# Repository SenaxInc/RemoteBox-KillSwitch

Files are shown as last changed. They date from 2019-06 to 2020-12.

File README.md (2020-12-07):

# RemoteBox-KillSwitch

## Overview:
  * Arduino attached to a liquid level height switch.
  * Arduino attached to an engine ignition.
  * When liquid switch is triggered, a radio signal is sent to turn of the engine.

## Main Parts:
  * Arduino Uno with Radio Shield
  * DIGI xbee LoRa Radios
  * Relay Switch Module
  * Solar Panel
  * Morningstar SunKeeper-6 Charge Controller
  * Lead Acid Battery

## Wiring Diagram - Solar



## Solder Diagram



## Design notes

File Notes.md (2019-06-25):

## ToDo

  * send confirmation signal back to level monitor box, use to trigger sleep
  * sleep mode
      * see avr sleep example: https://github.com/dorkmo/ArduinoSMSTankAlarm/blob/master/TankAlarm072017.ino
      * see digi sleep mode: https://www.digi.com/resources/documentation/Digidocs/90001456-13/reference/r_wk_sleep_mode.htm
  * syncronize sleep/wake times
      * wake up every 30 minutes, broadcast till other box wakes up, do the business, then sleep for 30 minutes 

## Questions

  * can an arduino digital pin put out enough amps to power the relay module?
      * could power down relay module when not in use

## Sleep Routine

  * when transmition of kill or stay alive broadcast is complete and confirmed.
      * send "Z" to say ready for bed. When recieve "z" back, end all transmissions.
      * xbee sleep mode will engage after 2 minutes as predefined time in XCTU settings
      * arduino will go into avr sleep mode for 8 seconds at a time, keeping count.
      * after 28 minutes wakeup xbee as defined in XCTU sleep timer
      * after 30 minutes, end arduino avr sleep.
      * Broadcast "W" awake status every 1 minute using delay(). wait for "w" confirmation.
      * Broadcast status of liquid level switch. "K" to kill. "A" to stay alive.
      * Wait for Confirmation of "k", "a", or "E" for error. 
      * Broadcast "Z"

## Related Links

  * http://opensourceecology.org/wiki/MicroTrac_Controller_v17.10/Code

## XBEE SETTINGS

  * NI - Name for Module
  * Sleep using arduino pin signal:
      * SM - 1
  * Sleep using timer:
      * SO - 8
      * ST - 493E0
      * SP - 249F0

  * http://docs.digi.com/display/XBeeArduinoCodingPlatform/Sleep+mode
  * https://www.digi.com/resources/documentation/Digidocs/90001477/reference/r_cmd_so.htm
  * http://cms.digi.com/resources/documentation/digidocs/90001537/references/r_xbee_sleeping_problems.htm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

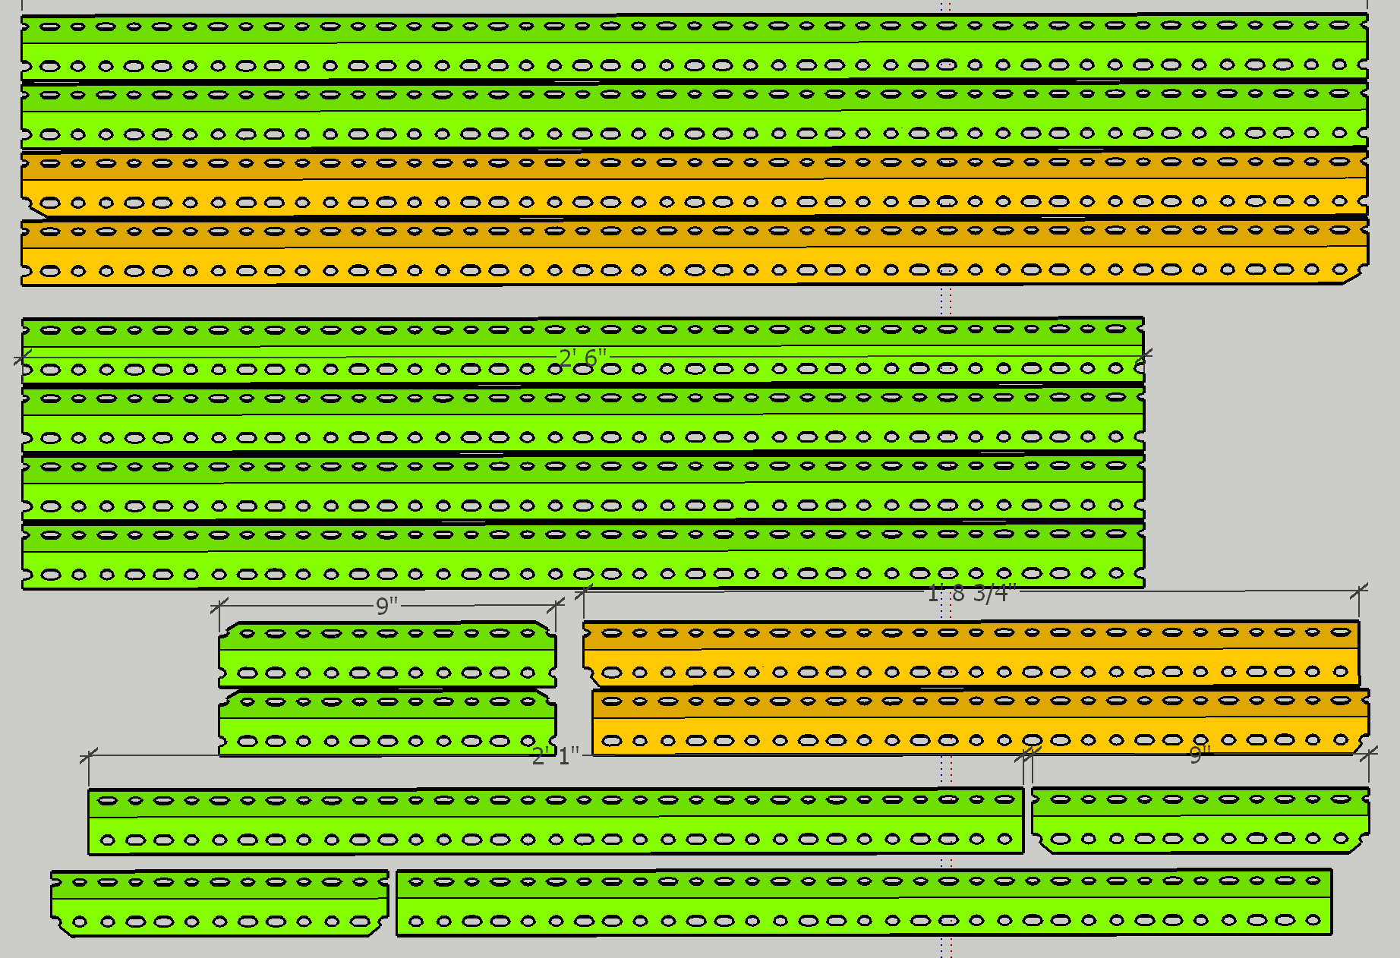
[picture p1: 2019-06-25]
SolarPanelStandCuts.png

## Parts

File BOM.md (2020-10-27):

## Common Parts
No. | Name | Link
--- | --- | ---
2 | SparkFun XBee Shield | https://www.mouser.com/ProductDetail/474-WRL-12847
2 | Arduino Stackable Header Kit | https://www.mouser.com/ProductDetail/375-LS-00010
1 | Jumper Wire M-M | https://www.mouser.com/ProductDetail/932-MIKROE-513
1 | Jumper Wire M-F | https://www.mouser.com/ProductDetail/932-MIKROE-512
2 | Panel Plug N-SMA | https://www.mouser.com/ProductDetail/455-34NSMA501193UE
2 | Cable 24" N-N | https://www.mouser.com/ProductDetail/549-CCN-MM-RG58-24
2 | Cable 6" SMA-SMA | https://www.mouser.com/ProductDetail/549-CCSMA-MM-086-6
2 | Adapter RP-SMA M - SMA F | https://www.mouser.com/ProductDetail/712-ADP-RPSM-SMAF
2 | Antenna 870-960 MHz | https://www.excel-wireless.com/900-mhz-omni-directional-antenna
2 | Arduino Uno | https://www.mouser.com/ProductDetail/Arduino/A000066
2 | Terminal Block | https://www.homedepot.com/p/Gardner-Bender-22-10-AWG-6-Circuit-Terminal-Block-1-Pack-GTB-406/202522482
1 | N.C. Float Switch | https://www.grainger.com/product/DAYTON-Float-Switch-3BY75

## Power Options
### Solar Option - Off Grid Engines
No. | Name | Link
--- | --- | ---
2 | SunKeeper-6 | https://www.solar-electric.com/mosupamoco6a.html
2 | Optima D31T | https://www.walmart.com/ip/OPTIMA-YellowTop-Dual-Purpose-Battery-Group-d31t/579876980
2 | 3.3V Zener Diode | https://www.mouser.com/ProductDetail/625-BZX55C3V3
2 | 330Ohm Resistor | https://www.mouser.com/ProductDetail/OK3315E-R52
1 | 5V Relay Module | https://www.robotshop.com/en/2-channel-5v-relay-module-elf.html

### 120V Power Line - Electric Motors
No. | Name | Link
--- | --- | ---
1 | Solid State Relay | https://www.grainger.com/product/CRYDOM-Solid-State-Relay-1DTK4
1 | 5V DC Power Supply | https://www.mouser.com/ProductDetail/436-PBA10F-5-N

## Radio Options
### Long Range Point to MultiPoint - Gauge within range of all cutoff points
No. | Name | Link
--- | --- | ---
2 | XBee Radio 902-928MHz XBP9B-DPST-001 | https://www.mouser.com/ProductDetail/888-XBP9B-DPST-001

### Short Range Mesh Network - Gauge not within range of all cutoff points
No. | Name | Link
--- | --- | ---
2 | XBee Radio 902-928MHz XBP9B-DMST-002 | https://www.mouser.com/ProductDetail/888-XBP9B-DMST-002

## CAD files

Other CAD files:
Solar Panel Stand 2018.skp

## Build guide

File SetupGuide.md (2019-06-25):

# XBee

Download XCTU
https://www.digi.com/resources/documentation/digidocs/90001458-13/default.htm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

Open XCTU

Plug in Xbee Explorer Dongle to computer - https://www.sparkfun.com/products/11697

Ctrl+Shft+D to search for radio

Change variables

NI - Set a discriptive name of location and cutoff or level 

SM - 1 pin sleep mode

ID - #### pick a network ID

Write down SH - Serial High and SL - Serial Low

Unplug 1st XBee and Install 2nd

Set the same parameters and enter the 1st's SH and SL into the DH - destination high and DL - destination low

Write down the SH and SL

Unplug 2nd xbee and plug in the 1st

Set the DH and DL as the SH and SL of the 2nd xbee

# Arduino

Upload code to arduinos

  * For the arduino monitoring the liquid level
      * https://create.arduino.cc/editor/dorkmo/c2d4928e-15f0-4c2c-a119-536aa2c805b0/preview
      * https://github.com/SenaxInc/RemoteBox-KillSwitch/blob/master/LoopTest-Level/LoopTest-Level.ino
  * For the arduino commanding the cut off relay
      * https://create.arduino.cc/editor/dorkmo/c1a42b12-49da-4830-a664-cde163ad2a28/preview
      * https://github.com/SenaxInc/RemoteBox-KillSwitch/blob/master/LoopTest-Cutoff/LoopTest-Cutoff.ino

Gather all the parts for the Sparkfun XBee Shield - https://www.sparkfun.com/products/12847

Solder the Resistor, Ziener Diode, and jumper wire to the as seen on diagram

Flip DLINE/UART switch to DLINE

Install the shields onto the arduinos

Install the XBee onto the shields

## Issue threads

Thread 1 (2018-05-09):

change ignition connection to Normally Closed

dorkmo, 2018-05-09:
iginition will be grounded until communication is established and steady power.
can arduino sleepmode power a pin while asleep?

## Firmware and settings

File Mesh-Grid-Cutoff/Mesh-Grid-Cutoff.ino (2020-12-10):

//periodically checks for radio message. If recieve kill signal, flip relay module. Send Confirmation that relay has been engaged.

///////////////////////////

#include <SoftwareSerial.h>  // SoftwareSerial used to communicate with the XBee from Arduino
// XBee's DOUT (TX) is connected to pin 2 (Arduino's Software RX)
// XBee's DIN (RX) is connected to pin 3 (Arduino's Software TX)
// SoftwareSerial XBee(2, 3); // RX, TX

////// VARIABLES //////

int confirmpin = 11;                 //define "read" Pin to confirm relay has been flipped

int relaypin = 10;                 //define "write" pins to control Relay module

int confirmstate = digitalRead(confirmpin);    //to handle data of current State of the relay

int bedtime = 0;              //1= its time for bed. 0= its time to stay awake.

int timeout = 0;

int tick8 = 0;

int sleeptick8s=75;   //how many sets of 8 seconds to wait before starting up again  225 


////// SETUP //////

void setup() {

pinMode(relaypin, OUTPUT); //SET PINS AS OUTPUT TO RELAY MODULE

digitalWrite(relaypin, LOW);  //ground ignition at startup for safety. verify connection before allowing engine to run.

pinMode(confirmpin,INPUT_PULLUP); //define liquid level pin mode

pinMode(13, OUTPUT);  //LED
  
//pinMode(9, OUTPUT); //XBee sleepmode pin. High=sleep. Low=awake.  

//digitalWrite(9, LOW);                 //wake up XBee
delay(2000);
  
Serial.begin(9600);                       //START COMMUNICATING WITH XBEE

    Serial.print('A');  

    digitalWrite(relaypin, LOW);  //blink twice
    delay(1000);
    digitalWrite(relaypin, HIGH);
    delay(1000);
    digitalWrite(relaypin, LOW);
    delay(1000);
    digitalWrite(relaypin, HIGH);
    delay(1000);
    digitalWrite(relaypin, LOW);
    delay(1000);  
  
    bedtime = 0;  //set bedtime to 0
  
}

///// LOOP /////

void loop() {

while (bedtime==0 && Serial.available()>0){               //if message available...
    
char RXbyte = char(Serial.read());        //read message...
  
  if (RXbyte == 'K') {                    //if message is "K"...
    digitalWrite(relaypin, LOW);               //close iginition circuit
    delay(10);
    confirmstate = digitalRead(confirmpin);
    if (confirmstate == HIGH){
    Serial.print('k');                    //send "k" message to confirm relay has been flipped
    timeout=1;
    } else {
    Serial.print('E');  
    }
  }
if (RXbyte == 'A') {                      //if message is "A"...
    digitalWrite(relaypin, HIGH);               //open iginition circuit
    delay(10);
    confirmstate = digitalRead(confirmpin);
    if (confirmstate == LOW){
    Serial.print('a');                    //send "k" message to confirm relay has been flipped
    timeout=1;
    } else {
    Serial.print('E');  
    }
  }

if (RXbyte == 'Z') {                      //when level box recieves confirmation is sends "Z" for "ready to sleep"
    Serial.print('z');                    //send "z" to confirm  "cut off ready to sleep"
    timeout=1;
  }

if (RXbyte == 'z') {
    delay(8000);
    bedtime=1;                           //initiate bedtime next loop
    timeout=1;
  }

} //end serial available while

  delay(5000);
  timeout++;
  
  if (timeout>720000) {                   //if timout count is greater than 1 hour....
    digitalWrite(relaypin, LOW);               //close iginition circuit, kill engine
    Serial.print('k');                    //send "k" message to confirm relay has been flipped
  }  
  

while (bedtime==1){
// digitalWrite(9, HIGH);                   //put XBee to sleep
 delay(8000);                             //wait 8 seconds
 tick8++;                                 //add 1 to "tick8"
 
//blink
    digitalWrite(13, HIGH);
    delay(500);
    digitalWrite(13, LOW);
//end blink
                           
  
if (tick8>sleeptick8s){                          //after 30 minutes...
    tick8=0;
    bedtime=0;                           //end bedtime
   digitalWrite(9, LOW);                 //wake up XBee
   
    digitalWrite(13, LOW);
    delay(1000);
    digitalWrite(13, HIGH);
    delay(2000);
    digitalWrite(13, LOW);
    delay(1000);
    digitalWrite(13, HIGH);
    delay(4000);
    digitalWrite(13, LOW);
    delay(1000);  
}                                        //end tick8 if  
  
} //end bedtime=1 while
  
} //end main loop

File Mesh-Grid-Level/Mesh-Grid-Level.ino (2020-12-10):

//used to monitor level height switch and send cut off signal to remote kill switch box. When recieve confirmation of cutoff, end sending message until level switch is reset.

///////////////////////

// We'll use SoftwareSerial to communicate with the XBee:
#include <SoftwareSerial.h>
// XBee's DOUT (TX) is connected to pin 2 (Arduino's Software RX)
// XBee's DIN (RX) is connected to pin 3 (Arduino's Software TX)
// SoftwareSerial XBee(2, 3); // RX, TX

////// VARIABLES //////

int lvlpin = 10; //liquid level switch set to Pin 10

int lvlstate = digitalRead(lvlpin);  //to handle data of current State of a switch

int bedtime = 0;

int tick8=0;

int sleeptick8s=75;   //how many sets of 8 seconds to wait before starting up again  225 

////// SETUP //////

void setup() {

pinMode(lvlpin,INPUT); //define liquid level pin mode
digitalWrite(lvlpin,HIGH);  //pin reads high when not connected to ground, will read low when connected to ground

pinMode(13, OUTPUT);  //LED
  
//pinMode(9, OUTPUT);  //XBee sleepmode pin. High=sleep. Low-awake.

Serial.begin(9600);      //START COMMUNICATING WITH XBEE  

//digitalWrite(9, LOW);                 //wake up XBee
delay(2000);                          //give it a few seconds to catch its breath
  
    Serial.print('A');  

    digitalWrite(13, LOW);  //blink twice
    delay(1000);
    digitalWrite(13, HIGH);
    delay(1000);
    digitalWrite(13, LOW);
    delay(1000);
    digitalWrite(13, HIGH);
    delay(1000);
    digitalWrite(13, LOW);
    delay(1000);  
  
    bedtime = 0;  //set bedtime to 0
  
  delay(5000);                              //wait 5 seconds    
}

//// LOOP ////

void loop() {
  
  
   // read the state of the switch into a local variable:
digitalWrite(lvlpin, HIGH);
delay(2000);
  lvlstate = digitalRead(lvlpin);
  delay(10);
  lvlstate = digitalRead(lvlpin);
delay(2000);
digitalWrite(lvlpin, LOW);

  if (lvlstate == HIGH) {       //If the state of the switch is "HIGH", AKA the N.C. switch is tripped...      
    Serial.print('K');   //Send the Kill Signal
    delay(5000);     
  } else {               //If the switch was not "HIGH"...
    Serial.print('A');   //Send Alive Signal
    delay(5000);     
  }
  
  bedtime=1;                           //initiate bedtime next loop

while (bedtime==1){
//    digitalWrite(9, HIGH);
 delay(8000);                             //wait 8 seconds
 tick8++;                                 //add 1 to "tick8"

//blink
    digitalWrite(13, HIGH);
    delay(500);
    digitalWrite(13, LOW);
//end blink
  
if (tick8>sleeptick8s){                          //after 30 minutes...
    tick8=0;
    bedtime=0;                           //end bedtime
      digitalWrite(9, LOW);
      
    digitalWrite(13, LOW);
    delay(1000);
    digitalWrite(13, HIGH);
    delay(1000);
    digitalWrite(13, LOW);
    delay(1000);
    digitalWrite(13, HIGH);
    delay(1000);
    digitalWrite(13, LOW);
    delay(1000);  
}                                        //end tick8 if  
  
} //end bedtime1 while

} //end main loop  

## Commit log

2018-06-07 added shield solder diagram
2019-04-08 new solar stand using slotted angle
2020-12-07 shorten time to 10 min
    [Mesh-Grid-Cutoff.ino, Mesh-Grid-Level.ino]
2020-12-09 comment out sleep pin for now
